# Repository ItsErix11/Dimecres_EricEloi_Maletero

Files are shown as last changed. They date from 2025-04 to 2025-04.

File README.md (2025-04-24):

View this project on [CADLAB.io](https://cadlab.io/project/29036). 

# Proyecto Maletero

## Autores
- Eric Trejo Sanchez (@ItsErix11)
- Eloi Ortega Ortiz (@EloiOrtega)

## Versió - v1.0 ## Curs - Assignatura de Disseny de PCBs amb KiCad - [Curs 2024-2025]

## Objetivo 
Nuestro objetivo es crear un sistema controlador del maletero de un coche que pueda cumplir las funciones de abrir y cerrar el maletero con un motor, desempañar el cristal de este y que se pueda abrir con un sensor con el pie en el caso de tener las manos ocupadas

## Requisitos i especificaciones
- Control del motor de apertura/cierre del maletero
- Sistema de calefacción para desempañar el cristal
- Sensor de movimiento para apertura sin contacto
- Interfaz CAN para comunicación con otros sistemas del coche
- Protección contra sobrecorriente en el control del motor

## Diagrama de bloques 
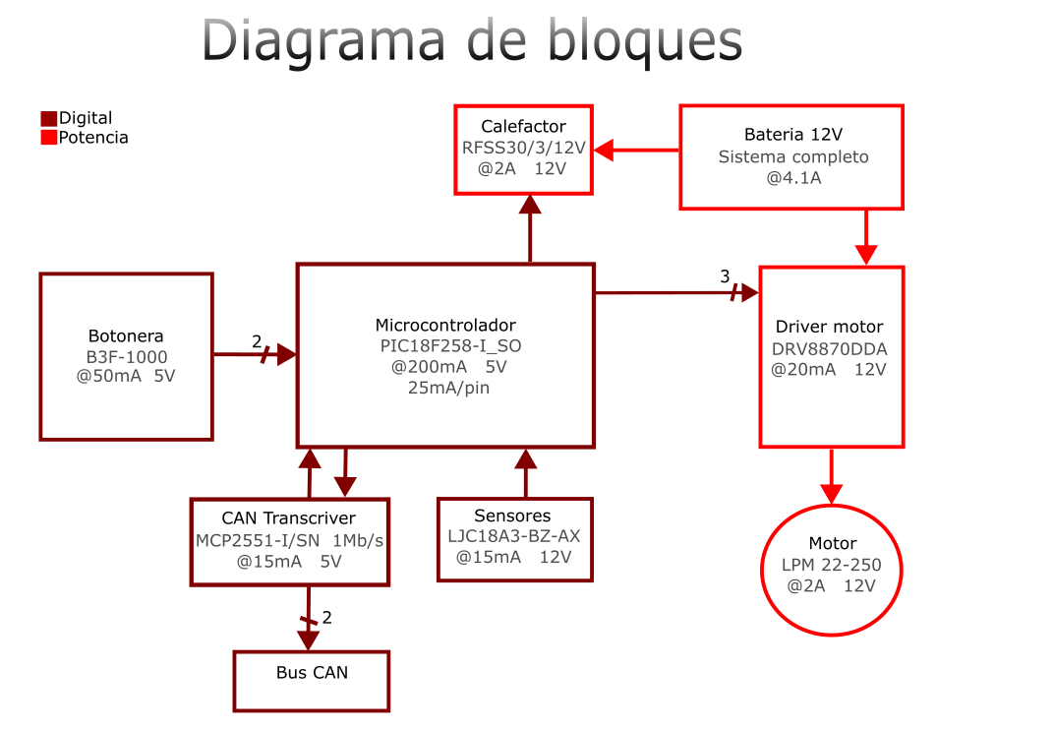
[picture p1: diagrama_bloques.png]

## Tabla de componentes
| Descripció | Manufacturer Number | Package | Datasheet | Proveïdor | Unitats |
|---|---|---|---|---|---|
| LDO Voltage Regulators 5A L Drop Pos Fixed Regs | LT1084CT-5 | TO-220 | https://eu.mouser.com/datasheet/2/609/1083ffe-3123432.pdf | DigiKey | 1 |
| MCU 32 KB FL 1536 RAM 25 I/O | PIC18F2580T-I/SO | SOIC-28 | https://eu.mouser.com/datasheet/2/268/39637d-3443674.pdf | DigiKey | 1 |
| Impulsor de motor Unipolar NMOS PWM 8-SO-PowerPad | DRV8870DDA | HTSSOP-8 | https://www.ti.com/lit/ds/symlink/drv8870.pdf?HQS=dis-dk-null-digikeymode-dsf-pf-null-wwe&ts=1745209885777 | DigiKey | 1 |
| CAN Interface IC Hi Spd CAN Transceiv | MCP2551-I/SN | SOIC-8 | https://eu.mouser.com/datasheet/2/268/20001667G-3441642.pdf | DigiKey | 1 |
| Operational Amplifiers - Op Amps LOW PWR SGL OP AMP A 926-LM321MF/NOPB | LM321MFX/NOPB | SOT-23-5 | https://www.ti.com/lit/ds/symlink/lm321.pdf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 | DigiKey | 1 |

## Funcionalidades
1. **Control del maletero**:
   - Apertura y cierre mediante motor controlado por el MCU
   - Protección antipinch mediante detección de corriente
   
2. **Sistema de desempañado**:
   - Calefacción controlada por botones para regulación de temperatura
   
3. **Apertura sin contacto**:
   - Sensor de movimiento para detección del pie

4. **Interfaz de comunicación**:
   - Protocolo CAN para integración con otros sistemas del coche
   - Posibilidad de control remoto desde la llave o panel central

## Historial de cambios 
| Data | Autor | Branch | Descripció |
|---|---|---|---|
| 2025-04-24 | Eric | `main` | Orden final, final del readme |
| 2025-04-24 | Eloi | `main` | Ultima revisión |
| 2025-04-23 | Eric | `main` | Version final final |
| 2025-04-23 | Eric | `main` | Todos los arreglos del placement |
| 2025-04-22 | Eric | `main` | Textos de fabrica y reglas de diseño solucionado |
| 2025-04-22 | Eric | `main` | Orden de carpetas y referencia a autores (nosotros) |
| 2025-04-21 | Eric | `main` | Inicio presupuesto y continuación del readme |
| 2025-04-18 | Eloi | `main` | Actualización del layout |
| 2025-04-17 | Eloi | `main` | Actualización del layout y netclases |
| 2025-04-12 | Eric | `main` | Orden carpetas |
| 2025-04-12 | Eric | `main` | Diagrama completo |
| 2025-04-09 | Eric | `main` | Esquematico final y pasado al layout |
| 2025-04-09 | Eric | `main` | Orden del esquematico |
| 2025-04-09 | Eric | `main` | Esquematico compactado |
| 2025-04-09 | Eloi | `main` | Corrección de errores de clase |
| 2025-04-09 | Eric | `main` | DRC errores 0, warnings 25 |
| 2025-04-09 | Eloi | `main` | Ultimos ajustes de islas del GND |
| 2025-04-08 | Eloi | `main` | Actualización de huella |
| 2025-04-08 | Eric | `main` | Reglas de diseño, 0 errores y separación de componentes |
| 2025-04-08 | Eric | `main` | Par diferencial CAN |
| 2025-04-08 | Eloi | `main` | Corrección de reglas de diseño del layout | 
| 2025-04-04 | Eloi | `main` | Layout v1.2 acabado |
| 2025-04-02 | Eloi | `main` | Corrección de errores del layout |
| 2025-04-02 | Eric | `main` | Esquematico y diagrama acabados |
| 2025-04-01 | Eloi | `main` | Layout final v.1, routing terminado |
| 2025-04-01 | Eric | `main` | Arreglos del GNDPWR y GND |
| 2025-04-01 | Eloi | `main` | Actualización del layout, capas top suprimidas |
| 2025-04-01 | Eric | `main` | Capas de cobre del layout y DE-9 |
| 2025-04-01 | Eloi | `main` | Actualización del layout |
| 2025-04-01 | Eloi | `main` | Layout placement |
| 2025-04-01 | Eloi | `main` | Creación del layout |
| 2025-04-01 | Eric | `main` | Arreglos esquemático |
| 2025-04-01 | Eloi | `main` | Huellas añadidas al esquematico |
| 2025-04-01 | Eloi | `main` | Cambio de sensor en el esquemático |
| 2025-03-31 | Eric | `main` | Adición del DE-9 y regulador del sensor del esquemático|
| 2025-03-30 | Eloi | `main` | Corrección de errores del esquemático |
| 2025-03-30 | Eric | `main` | Esquemático ordenado |
| 2025-03-29 | Eloi | `main` | Corrección del switch y net lists del esquemático |
| 2025-03-29 | Eric | `main` | Mas correcciones del esquemático |
| 2025-03-27 | Eric | `main` | Correcciones de orden y conectores del esquemático|
| 2025-03-26 | Eloi | `main` | Adición de Net lists, corrección de errores y regulador de tensión del esquematico |
| 2025-03-25 | Eric | `main` | Conector del Program |
| 2025-03-25 | Eric | `main` | Diagrama de bloques añadido |
| 2025-03-25 | Eric | `main` | Rth mas disperso |
| 2025-03-25 | Eric | `main` | Corrección del CAN y separación |
| 2025-03-25 | Eric | `main` | Adición de condensadores de desacoplo |
| 2025-03-25 | Eloi | `main` | Versión casi final |
| 2025-03-25 | Eric | `main` | Transcriver CAN, casi todo el MCU completado |
| 2025-03-24 | Eloi | `main` | Corrección de errores |
| 2025-03-24 | Eloi | `main` | Resistencia termica añadida |
| 2025-03-24 | Eric | `main` | Pruebas del proyecto |
| 2025-03-24 | Eric | `main` | Cristal añadido |
| 2025-03-24 | Eric | `main` | Reorganización y corrección de errores |
| 2025-03-24 | Eloi | `main` | Etapa de regulación (LT1117) |
| 2025-03-24 | Eric | `main` | Adición de conectores |
| 2025-03-24 | Eric | `main` | Creación del proyecto |

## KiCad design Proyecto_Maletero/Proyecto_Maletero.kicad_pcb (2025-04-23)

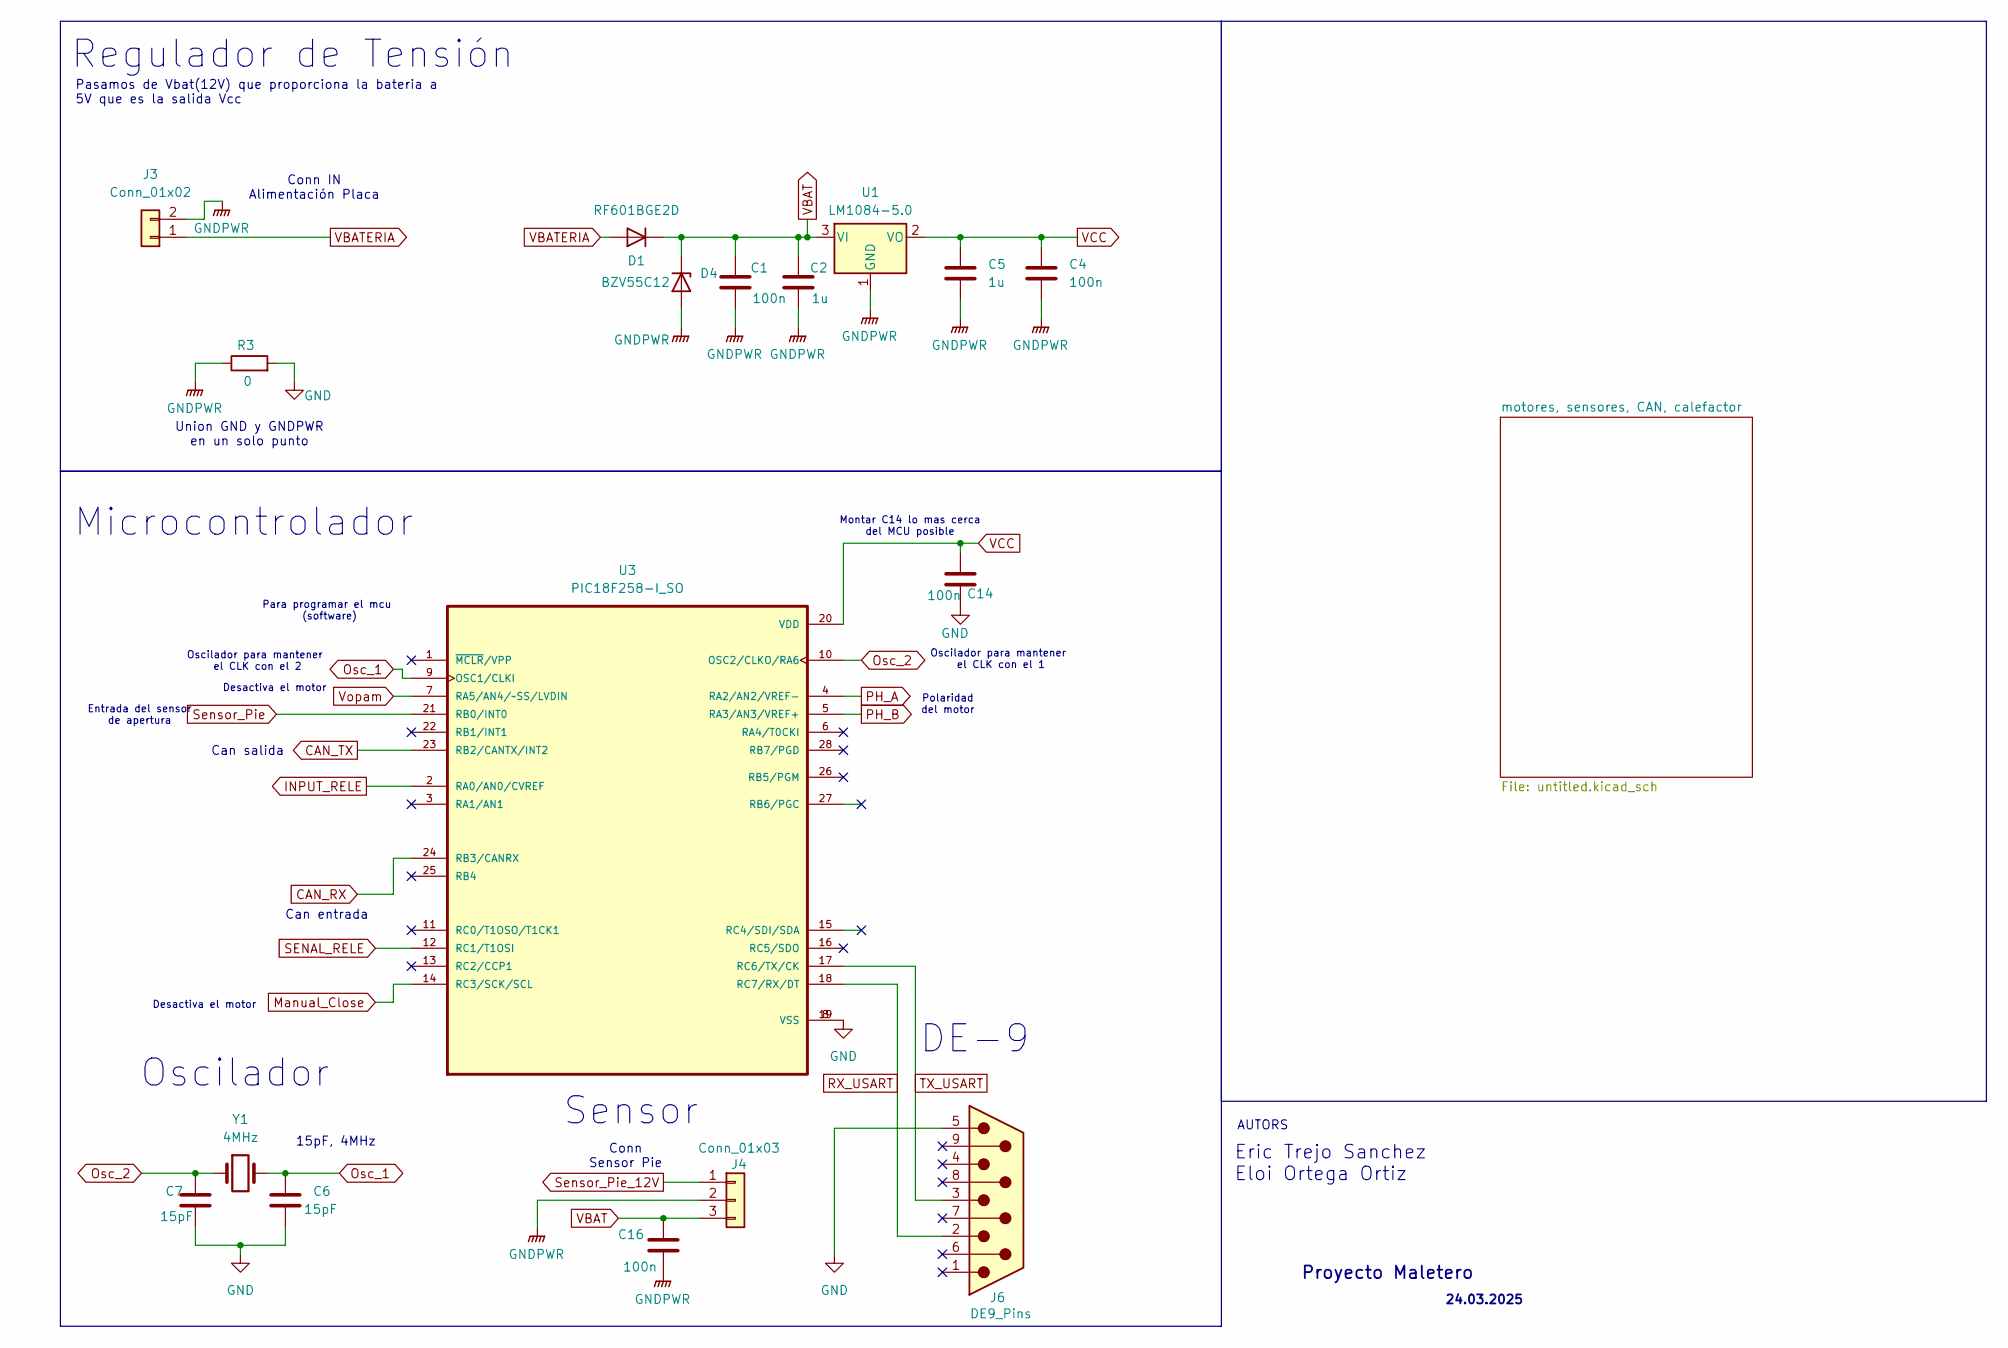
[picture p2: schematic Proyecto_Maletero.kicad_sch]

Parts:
C1, C4, C14, C16: 100n; C_0805_2012Metric
C2, C5: 1u; C_0805_2012Metric
C6, C7: 15pF; C_0805_2012Metric
D1: RF601BGE2D; D_0805_2012Metric
D4: BZV55C12; D_MiniMELF
J3: Conn_01x02; TerminalBlock_Phoenix_MKDS-1,5-2-5.08_1x02_P5.08mm_Horizont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
J4: Conn_01x03; TerminalBlock_Phoenix_MKDS-1,5-3_1x03_P5.00mm_Horizontal
J6: DE9_Pins; DSUB-9_Pins_Horizontal_P2.77x2.54mm_EdgePinOffset9.40mm
R3: 0
U1: LM1084-5.0; LT1117
U3: PIC18F258-I_SO; SOIC127P1030X265-28N
Y1: 4MHz; Crystal_SMD_HC49-SD

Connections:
CAN_RX: U3.24 (RB3/CANRX); also elsewhere on the board
CAN_TX: U3.23 (RB2/CANTX/INT2); also elsewhere on the board
GND: C6.2, C7.2, C14.1, J6.5, R3.2, U3.8 (VSS), U3.19 (VSS); also elsewhere on the board
GNDPWR: C1.2, C2.2, C4.2, C5.2, C16.1, D4.2 (A), J3.2, J4.2, R3.1, U1.1 (GND); also elsewhere on the board
INPUT_RELE: U3.2 (RA0/AN0/CVREF); also elsewhere on the board
Manual_Close: U3.14 (RC3/SCK/SCL); also elsewhere on the board
Osc_1: C6.1, U3.9 (OSC1/CLKI), Y1.2
Osc_2: C7.1, U3.10 (OSC2/CLKO/RA6), Y1.1
PH_A: U3.4 (RA2/AN2/VREF-); also elsewhere on the board
PH_B: U3.5 (RA3/AN3/VREF+); also elsewhere on the board
RX_USART: J6.2, U3.18 (RC7/RX/DT)
SENAL_RELE: U3.12 (RC1/T1OSI); also elsewhere on the board
Sensor_Pie: U3.21 (RB0/INT0); also elsewhere on the board
Sensor_Pie_12V: J4.1; also elsewhere on the board
TX_USART: J6.3, U3.17 (RC6/TX/CK)
VBAT: C1.1, C2.1, C16.2, D1.1 (K), D4.1 (K), J4.3, U1.3 (VI); also elsewhere on the board
VBATERIA: D1.2 (A), J3.1
VCC: C4.1, C5.1, C14.2, U1.2 (VO), U3.20 (VDD); also elsewhere on the board
Vopam: U3.7 (RA5/AN4/~SS/LVDIN); also elsewhere on the board

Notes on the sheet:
Desactiva el motor
Para programar el mcu (software)
Polaridad del motor
Eric Trejo Sanchez Eloi Ortega Ortiz
DE-9
Regulador de Tensión
Pasamos de Vbat(12V) que proporciona la bateria a 5V que es la salida Vcc
Microcontrolador
Sensor
Union GND y GNDPWR en un solo punto
15pF, 4MHz
Oscilador para mantener el CLK con el 1
Entrada del sensor de apertura
Can salida
Oscilador
Proyecto Maletero
Montar C14 lo mas cerca del MCU posible
Can entrada
AUTORS
24.03.2025
Oscilador para mantener el CLK con el 2
Conn IN Alimentación Placa
Conn Sensor Pie

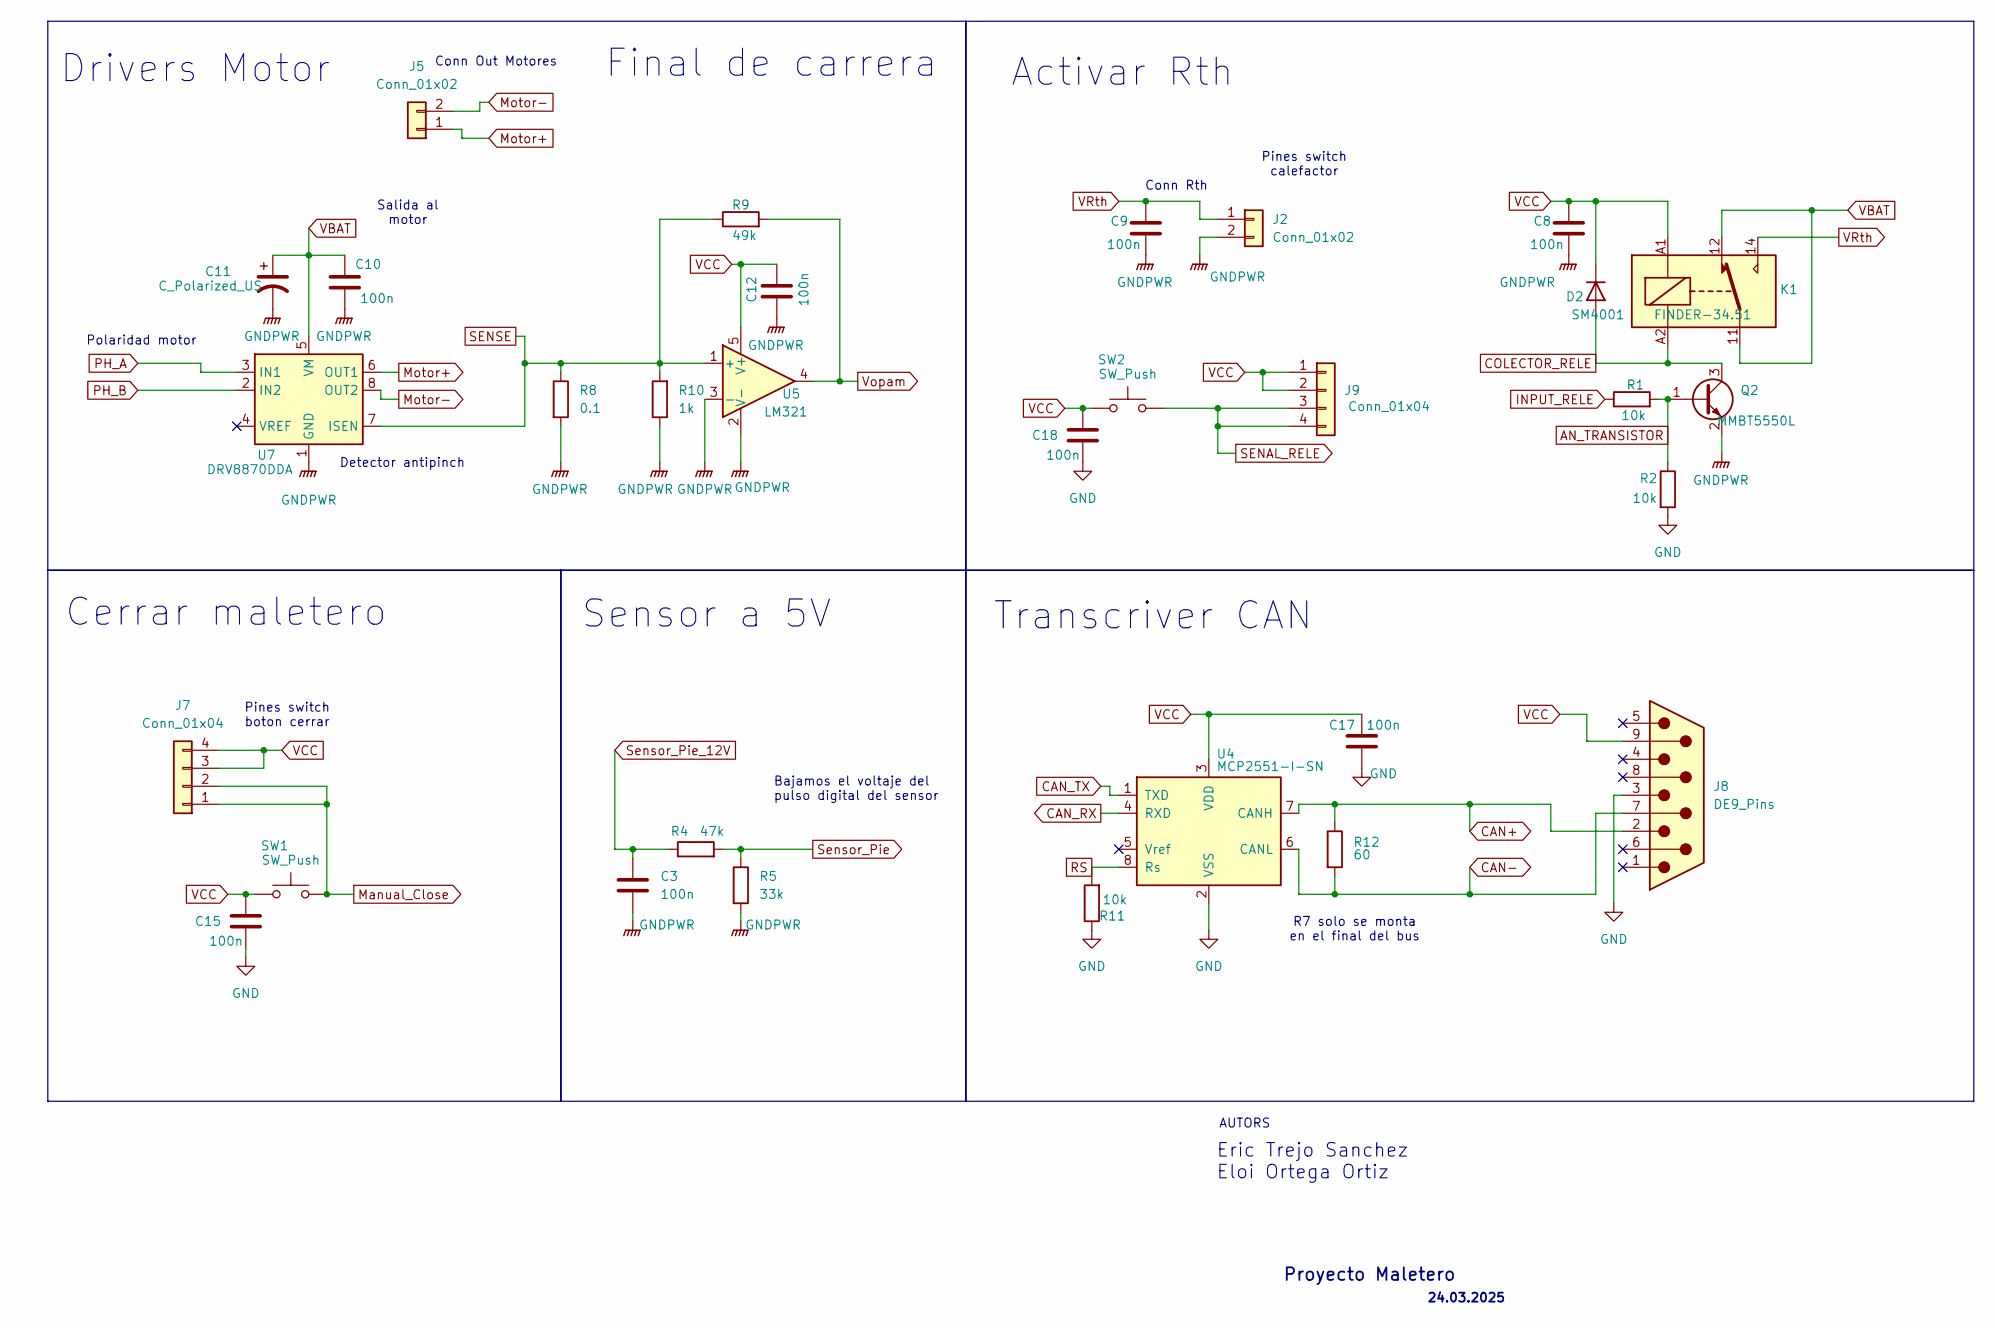
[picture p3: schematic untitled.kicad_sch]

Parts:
C3, C8, C9, C10, C12, C15, C17, C18: 100n; C_0805_2012Metric
C11: C_Polarized_US; CP_Elec_3x5.3
D2: SM4001; D_MELF
J2, J5: Conn_01x02; TerminalBlock_Phoenix_MKDS-1,5-2-5.08_1x02_P5.08mm_Horizont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
J7, J9: Conn_01x04; PinHeader_1x04_P2.54mm_Vertical
J8: DE9_Pins; DSUB-9_Pins_Horizontal_P2.77x2.54mm_EdgePinOffset9.40mm
K1: FINDER-34.51; Relay_SPDT_Finder_34.51_Vertical
Q2: MMBT5550L; SOT-23
R1, R2, R11: 10k; R_0805_2012Metric
R4: 47k; R_0805_2012Metric
R5: 33k; R_0805_2012Metric
R8: 0.1; R_0805_2012Metric
R9: 49k; R_0805_2012Metric
R10: 1k; R_0805_2012Metric
R12: 60; R_0805_2012Metric
SW1, SW2: SW_Push
U4: MCP2551-I-SN; SOIC-8_3.9x4.9mm_P1.27mm
U5: LM321; SOT-23-5
U7: DRV8870DDA; Texas_HTSOP-8-1EP_3.9x4.9mm_P1.27mm_EP2.95x4.9mm_Mask2.4x3.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

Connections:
AN_TRANSISTOR: Q2.1 (B), R1.2, R2.1
CAN+: J8.2, R12.1, U4.7 (CANH)
CAN-: J8.7, R12.2, U4.6 (CANL)
CAN_RX: U4.4 (RXD); also elsewhere on the board
CAN_TX: U4.1 (TXD); also elsewhere on the board
COLECTOR_RELE: D2.2 (A), K1.A2, Q2.3 (C)
GND: C15.1, C17.1, C18.1, J8.3, R2.2, R11.1, U4.2 (VSS); also elsewhere on the board
GNDPWR: C3.2, C8.2, C9.2, C10.1, C11.2, C12.2, J2.2, Q2.2 (E), R5.2, R8.2, R10.1, U5.2 (V-), U5.3 (-), U7.1 (GND), U7.9 (GND); also elsewhere on the board
INPUT_RELE: R1.1; also elsewhere on the board
Manual_Close: J7.1, J7.2, SW1.2; also elsewhere on the board
Motor+: J5.1, U7.6 (OUT1)
Motor-: J5.2, U7.8 (OUT2)
PH_A: U7.3 (IN1); also elsewhere on the board
PH_B: U7.2 (IN2); also elsewhere on the board
RS: R11.2, U4.8 (Rs)
SENAL_RELE: J9.3, J9.4, SW2.2; also elsewhere on the board
SENSE: R8.1, R9.1, R10.2, U5.1 (+), U7.7 (ISEN)
Sensor_Pie: R4.2, R5.1; also elsewhere on the board
Sensor_Pie_12V: C3.1, R4.1; also elsewhere on the board
VBAT: C10.2, C11.1, K1.11, K1.12, U7.5 (VM); also elsewhere on the board
VCC: C8.1, C12.1, C15.2, C17.2, C18.2, D2.1 (K), J7.3, J7.4, J8.9, J9.1, J9.2, K1.A1, SW1.1, SW2.1, U4.3 (VDD), U5.5 (V+); also elsewhere on the board
VRth: C9.1, J2.1, K1.14
Vopam: R9.2, U5.4; also elsewhere on the board

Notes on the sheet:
Transcriver CAN
Pines switch boton cerrar
Polaridad motor
R7 solo se monta en el final del bus
Final de carrera
Salida al motor
Drivers Motor
Activar Rth
AUTORS
24.03.2025
Proyecto Maletero
Detector antipinch
Cerrar maletero
Pines switch calefactor
Conn Out Motores
Sensor a 5V
Conn Rth
Eric Trejo Sanchez Eloi Ortega Ortiz
Bajamos el voltaje del pulso digital del sensor

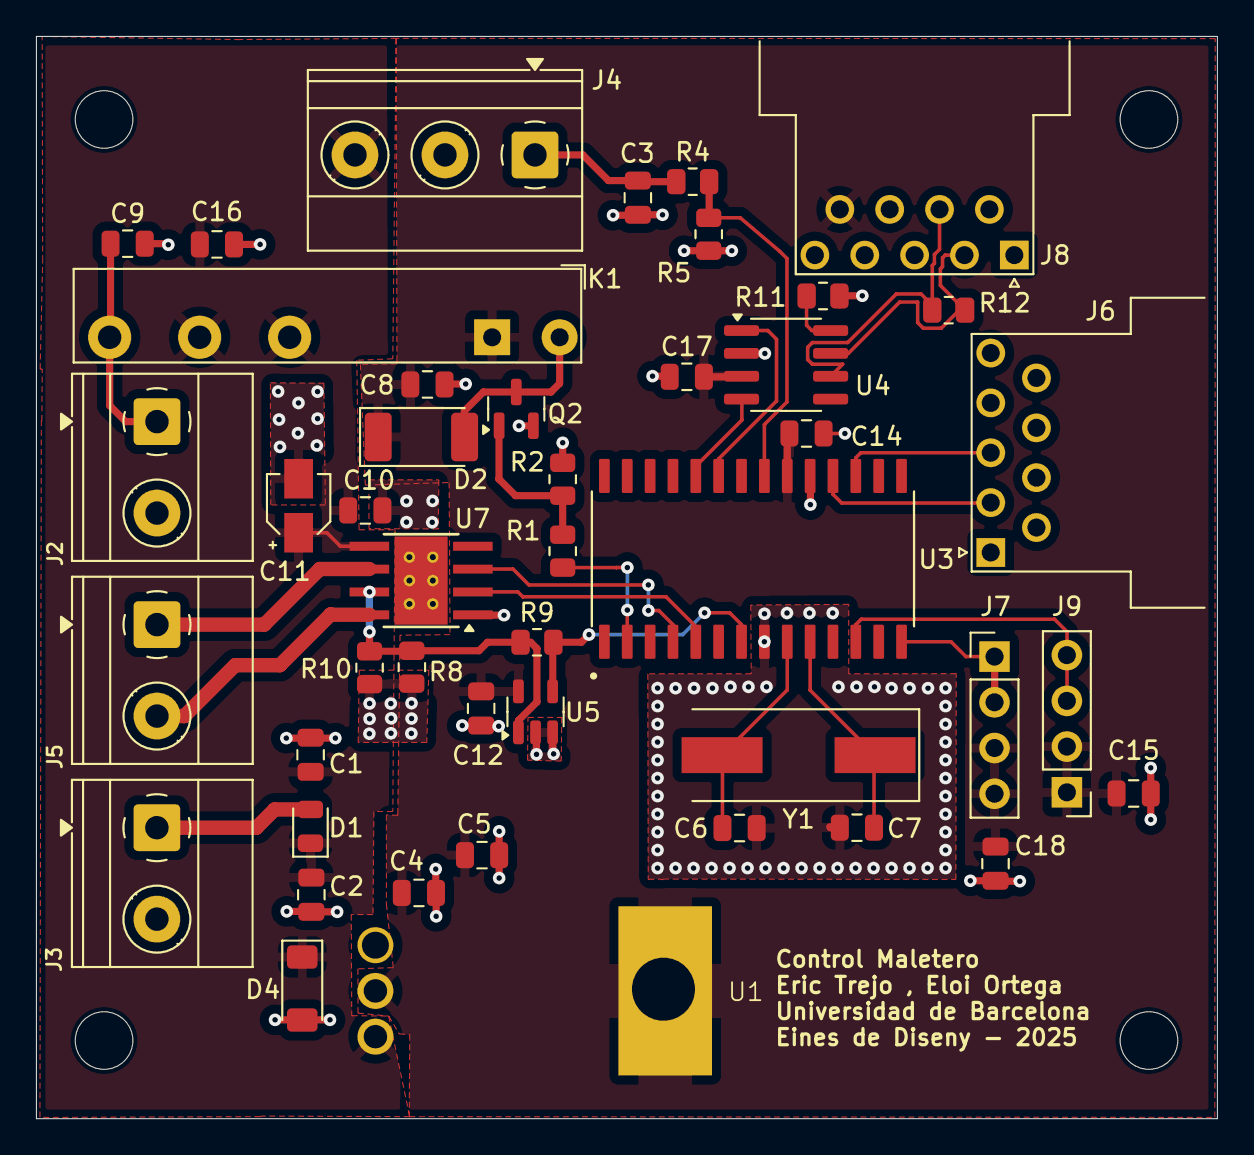
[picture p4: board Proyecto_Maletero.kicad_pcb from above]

Board: 2 copper layers, 65.6 x 60.1 mm, 45 parts (0 on the bottom side), 28 nets.

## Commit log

2025-03-24 Creación proyecto
    [Proyecto_Maletero.kicad_pcb, Proyecto_Maletero.kicad_sch]
2025-03-24 Eliminación proyecto
    [Proyecto_Maletero.kicad_pcb, Proyecto_Maletero.kicad_sch]
2025-03-24 Adición conectores
    [Proyecto_Maletero.kicad_sch]
2025-03-24 Etapa de regulacion (LT1117)
    Hemos añadido una etapa de regulación de VBAT.
    [Proyecto_Maletero.kicad_sch]
2025-03-24 Compracion guardado
    [Proyecto_Maletero.kicad_sch]
2025-03-24 Comprobación Guardado 2
    [Proyecto_Maletero.kicad_sch]
2025-03-24 Reorganizacion y correccion de errores
    [Proyecto_Maletero.kicad_sch]
2025-03-25 Cristal added
    Tengo que añadir las etiquetas del mcu
    [Proyecto_Maletero.kicad_sch]
2025-03-25 Pines MCU y anotaciones
    Tengo que mirar la freq de funcionamiento para nuestro sistema y confirmar los pines que faltan
    [Proyecto_Maletero.kicad_sch]
2025-03-25 Prueba 2
    [Proyecto_Maletero.kicad_sch]
2025-03-25 Resistencia Termica
2025-03-25 Correccion de errores
    [Proyecto_Maletero.kicad_sch]
2025-03-25 Etiquetas motor acabado
    Faltarian componentes pasivos
2025-03-25 Transcriver CAN, caso todo mcu
    Falta final de carrera
    [Proyecto_Maletero.kicad_sch]
2025-03-25 Version casi final
    Anadiodo, final de carrera, seleccion de pines, y condensadores de desacoplamiento
    [Proyecto_Maletero.kicad_sch]
2025-03-25 Corrección CAN y separación
    Hemos puesto una resistencia para los extremos del bus CAN. Tambien hemos separado los tags para que no se vea tan junto
    [Proyecto_Maletero.kicad_sch]
2025-03-25 Rth menos enano
    Hemos expandido Rth
    [Proyecto_Maletero.kicad_sch]
2025-03-26 Añadido diagrama de bloques
2025-03-26 Añadir NET list,modificacion de erros,, y regulador
    [Proyecto_Maletero.kicad_sch]
2025-03-27 Cambio de orden y posición de conn
    Tambien he añadido los DE-9, creo que el USART necesita un convertidor o algo asi, igual lo quitamos.
    [Proyecto_Maletero.kicad_sch]
2025-03-29 Correcciones de la version anterior
    Falta cambiar los nets múltiples esos
    [Proyecto_Maletero.kicad_sch]
2025-03-29 Mas correcciones
    Final de carrera, etc.
    [Proyecto_Maletero.kicad_sch]
2025-03-29 Correccion switch y anadido las net list
    Hemos anadido un rele y un npn para controlar la Rth
    [Proyecto_Maletero.kicad_sch]
2025-03-30 Correccion errores
    [Proyecto_Maletero.kicad_sch]
2025-03-31 DE-9 UART, regulador sensor, quitar program
    El program no se pone porque se programa a parte segun se dijo en clase
2025-03-31 Lo mismo pero guardando el proyecto
    Solo queda hacer la etapa de regulación del sensor y entramos al layout
    [Proyecto_Maletero.kicad_sch]
2025-03-31 auctualizacion y cambio de sensor
    [Proyecto_Maletero.kicad_sch]
2025-03-31 Añadido huellas
    [Proyecto_Maletero.kicad_sch]
2025-03-31 Comiezo layaut
    [Proyecto_Maletero.kicad_pcb, Proyecto_Maletero.kicad_sch]
2025-03-31 Layout inicio
    [Proyecto_Maletero.kicad_pcb, Proyecto_Maletero.kicad_sch]
2025-04-01 Capas y DE-9
    [Proyecto_Maletero.kicad_pcb]
2025-04-01 Actulizacion layout
    [Proyecto_Maletero.kicad_pcb, Proyecto_Maletero.kicad_sch]
2025-04-01 Layout final v.1
    [Proyecto_Maletero.kicad_pcb, Proyecto_Maletero.kicad_sch]
2025-04-02 esquematico acabado y diagrama acabado
    [Proyecto_Maletero.kicad_sch]
2025-04-02 Actualizaciones y primeros pasos para correfir errores
    [Proyecto_Maletero.kicad_pcb]
2025-04-04 Layout v1.2 acabado
    [Proyecto_Maletero.kicad_pcb, Proyecto_Maletero.kicad_sch]
2025-04-08 Correcion de reglas de diseno
    [Proyecto_Maletero.kicad_pcb]
2025-04-08 Cerrar KICAD
2025-04-08 nets par diferencial
    [Proyecto_Maletero.kicad_pcb]
2025-04-08 Reglas de diseño, errores 0, separación del transcriver
    hay 108 warnings igualmente
    [Proyecto_Maletero.kicad_pcb]
2025-04-08 Algun cambio
    [Proyecto_Maletero.kicad_pcb]
2025-04-08 Actualizacion de huella y errores
    [Proyecto_Maletero.kicad_pcb]
2025-04-08 Ultimos ajustes de islas de gnd y huellas
    [Proyecto_Maletero.kicad_pcb]
2025-04-09 DRC errores 0 warnings 25
    [Proyecto_Maletero.kicad_pcb]
2025-04-09 Correccion de errores en clase
    [Proyecto_Maletero.kicad_pcb, Proyecto_Maletero.kicad_sch]
2025-04-09 Modificaciones de Clase
    [Proyecto_Maletero.kicad_pcb]
2025-04-09 Esquematico compactado
    [Proyecto_Maletero.kicad_sch, untitled.kicad_sch]
2025-04-09 Modificación del orden del esquematico
    puesto a punto
    [Proyecto_Maletero.kicad_sch]
2025-04-09 Esquematico final y pasado al layout
    [Proyecto_Maletero.kicad_pcb, Proyecto_Maletero.kicad_sch]
2025-04-12 Orden carpetas
    [Proyecto_Maletero.kicad_pcb, Proyecto_Maletero.kicad_sch, untitled.kicad_sch]
2025-04-17 Actualizacion layout
    Colocacion idonias de tornillos, simetrias y reduccion de avisos de 8 a 2
    [Proyecto_Maletero.kicad_pcb, untitled.kicad_sch]
2025-04-17 NETCLASES
    Acabdo de modificar las net clases
2025-04-18 Actulizacion Placa
    Mover de9
    [Proyecto_Maletero.kicad_pcb]
2025-04-22 Orden de carpetas, referencia a los autores layout (nosotros)
    [Proyecto_Maletero.kicad_pcb]
2025-04-22 Textos del fabricante y error de reglas de diseño solucionado
    [Proyecto_Maletero.kicad_pcb]
2025-04-23 Muchos arreglos de placement
    [Proyecto_Maletero.kicad_pcb]
2025-04-23 Version final final
    [Proyecto_Maletero.kicad_pcb, untitled.kicad_sch]
2025-04-23 Ultimos cambios y revisiones
    [Proyecto_Maletero.kicad_pcb, Proyecto_Maletero.kicad_sch, untitled.kicad_sch]
